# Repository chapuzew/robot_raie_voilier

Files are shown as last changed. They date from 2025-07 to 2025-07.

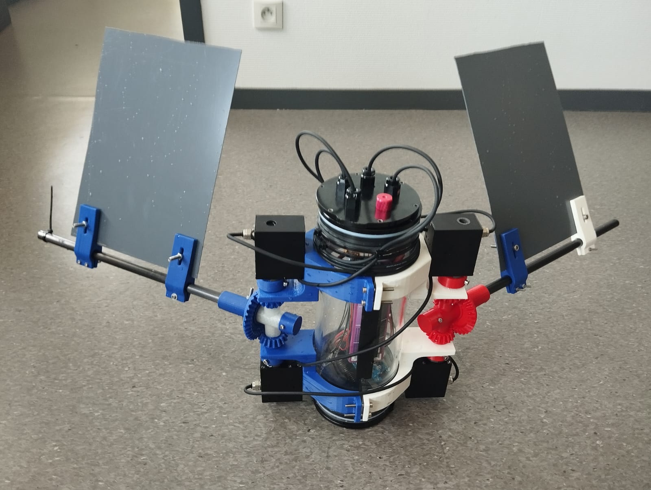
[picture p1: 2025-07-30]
robot_raie.jpg

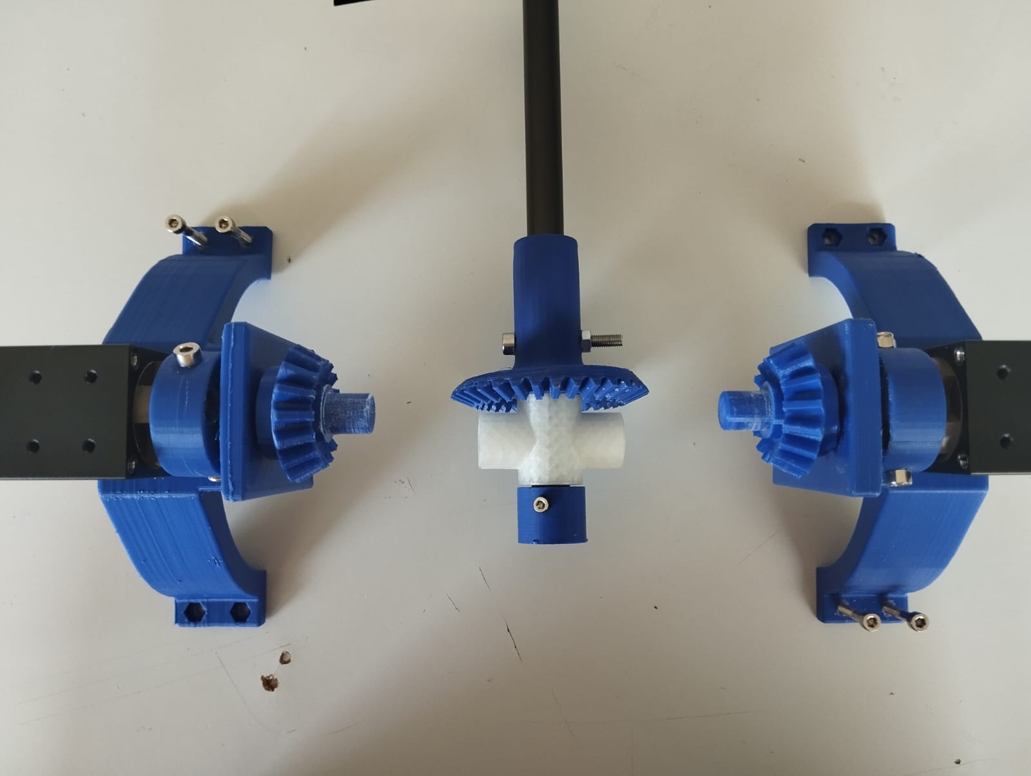
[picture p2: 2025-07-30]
videos-photos/WhatsApp Image 2025-07-22 à 16.33.31_99630c48.jpg

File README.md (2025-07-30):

Ce projet a etait réalisé dans le cadre de ma première année du Master Robotique Aquatique Mobile de l’ENSTA (École nationale supérieure de techniques avancées) Bretagne. Il présente les travaux menés lors d’un stage réalisé au sein du laboratoire de recherche STIC (Laboratoire des Sciences et Technologies de l'Information, de la Communication et de la Connaissance), à Brest, et porte sur le développement d’un prototype de robot bio-inspiré capable d’évoluer dans deux environnements distincts : en surface, à la manière d’un voilier, et sous l’eau, par nage ondulatoire inspirée des raies.
L’objectif principal de ce travail était de concevoir, fabriquer et tester un système capable de combiner ces deux modes de locomotion dans un même robot. L’approche retenue est bio-inspirée, dans le sens où elle s’appuie sur des principes naturels de déplacement, sans chercher à reproduire fidèlement une morphologie existante.
Ce travail avait pour but de déterminer si un prototype fonctionnel combinant ces deux modes de déplacement pouvait constituer une base pertinente pour un développement plus poussé. Une attention particulière a été portée à la conception mécanique, en intégrant dès le départ une contrainte de fabrication locale : toutes les pièces du robot devaient être réalisables via impression 3D ou usinage CNC, en utilisant les moyens disponibles sur place.
Le présent document retrace l’ensemble des étapes de développement, depuis la conception mécanique initiale jusqu’aux expérimentations finales en milieu aquatique. Il détaille également l’architecture électronique embarquée, les choix logiciels effectués (communication, contrôle des moteurs), ainsi que les observations et pistes d’amélioration identifiées à l’issue des essais en bassin.

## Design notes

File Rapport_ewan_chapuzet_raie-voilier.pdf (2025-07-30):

# Prototype d’un robot hybride de navigation multi-milieux : propulsion ondulatoire et voiles

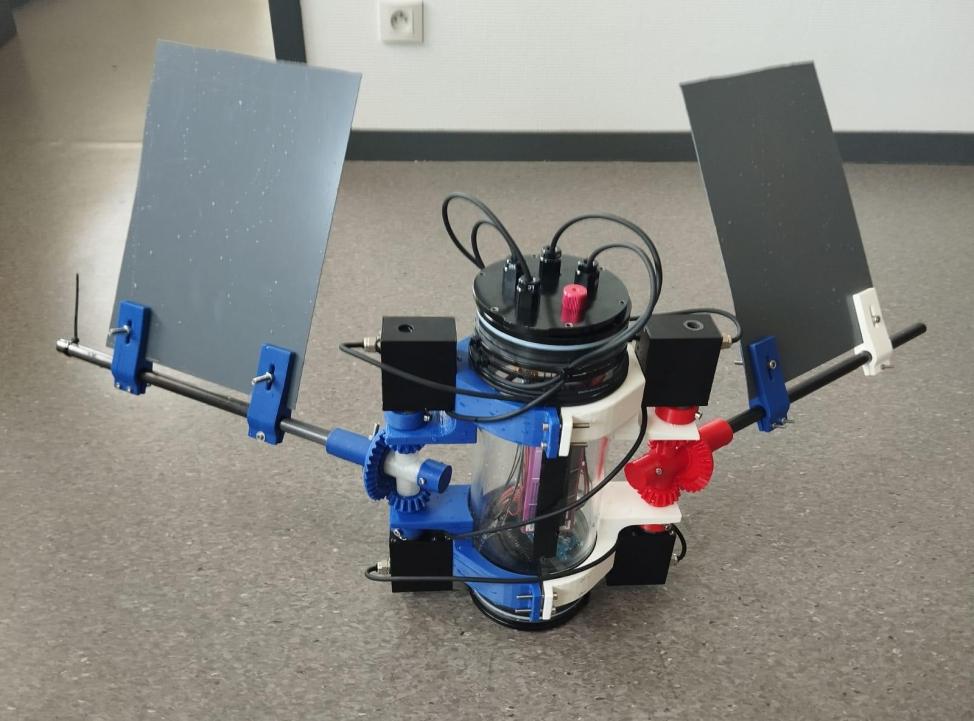
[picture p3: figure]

Figure 1 : Robot raie-voilier
Ce rapport s’inscrit dans le cadre de ma première année du Master Robotique Aquatique Mobile de l’ENSTA (École nationale supérieure de techniques avancées) Bretagne. Il présente les travaux menés lors d’un stage réalisé au sein du laboratoire de recherche STIC (Laboratoire des Sciences et Technologies de l'Information, de la Communication et de la Connaissance), à Brest, sous la supervision de Loick Degorre et Lionel Lapierre. Ce stage porte sur le développement d’un prototype de robot bio-inspiré capable d’évoluer dans deux environnements distincts : en surface, à la manière d’un voilier, et sous l’eau, par nage ondulatoire inspirée des raies. L’objectif principal de ce travail était de concevoir, fabriquer et tester un système capable de combiner ces deux modes de locomotion dans un même robot. L’approche retenue est bio-inspirée, dans le sens où elle s’appuie sur des principes naturels de déplacement, sans chercher à reproduire fidèlement une morphologie existante.
Ce travail avait pour but de déterminer si un prototype fonctionnel combinant ces deux modes de déplacement pouvait constituer une base pertinente pour un développement plus poussé. Une attention particulière a été portée à la conception mécanique, en intégrant dès le départ une contrainte de fabrication locale : toutes les pièces du robot devaient être réalisables via impression 3D ou usinage CNC, en utilisant les moyens disponibles sur place.
Le présent document retrace l’ensemble des étapes de développement, depuis la conception mécanique initiale jusqu’aux expérimentations finales en milieu aquatique. Il détaille également l’architecture électronique embarquée, les choix logiciels effectués (communication, contrôle des moteurs), ainsi que les observations et pistes d’amélioration identifiées à l’issue des essais en bassin.

## 1. Prototypage physique du Robot raie-voilier

### 1.1Conception mécanique de l’épaule

Le développement du robot raie-voilier a débuté par le prototypage mécanique de ses deux épaules, placées symétriquement de part et d’autre du tube principal. Inspirée de la nage ondulatoire des raies, cette conception s’inscrit dans une démarche bio-inspirée visant à exploiter les principes naturels de propulsion grâce à des ailes.
Matériaux et composants à disposition Le corps central du robot est constitué d’un tube étanche en polycarbonate de 4 pouces de diamètre et de 30 cm de longueur, fourni avec ses deux embouts ("end caps") et brides ("flanges") compatibles de marque Blue Robotics. Le montage a été réalisé selon les recommandations du Watertight Enclosure User Guide, (https://bluerobotics.com/learn/watertight-enclosure-wte-assembly-new/) garantissant une bonne étanchéité.
L’actionnement des ailes repose sur quatre servomoteurs étanches Rovmaker RM-SV-40, répartis équitablement sur les deux épaules. Les ailes ont été découpées dans des plaques de PVC de 1 mm d’épaisseur. Afin d’optimiser l’adhérence entre les pièces imprimées en 3D et le tube central, des bandes de caoutchouc de 1,5 mm ont été utilisées comme interface souple. Remarque importante : Toutes les pièces imprimées en 3D doivent impérativement respecter les paramètres définis dans la photo "parametres_impression", notamment avec un remplissage à 80 % et avec un motif gyroïde, afin d'assurer une bonne résistance mécanique. Il est également essentiel de veiller à l’orientation correcte des pièces comportant des engrenages lors de l’impression : les dents doivent impérativement être orientées vers le haut, pour garantir une meilleure précision et robustesse de l’ensemble.
Conception de l’épaule
Chaque épaule est conçue pour offrir deux degrés de liberté, dans le but d’explorer une large gamme de configurations tout en limitant la complexité mécanique. Le principe de rotation utilisé s’inspire du mécanisme présenté par thang010146 dans sa vidéo YouTube intitulée “Controlling pan and tilt rotation of an object”.
Les pièces de liaison entre les épaules et le tube central reprennent les principes des clamps Blue Robotics, assurant une fixation solide. Le montage complet est documenté dans le fichier d’assemblage “robot_raie_voilier”, qui répertorie l’ensemble des éléments mécaniques nécessaires, à l’exception de l’électronique, du câble de communication (tether 7 fils), des matériaux d’étanchéité et du filament d’impression 3D.
Améliorations mécaniques
Dans une première version, le mécanisme original a été simplifié par la suppression des courroies, remplacées par un contact direct entre pièces imprimées. Bien que ce système ait montré un fonctionnement correct, il s’est avéré trop fragile pour supporter des efforts importants.

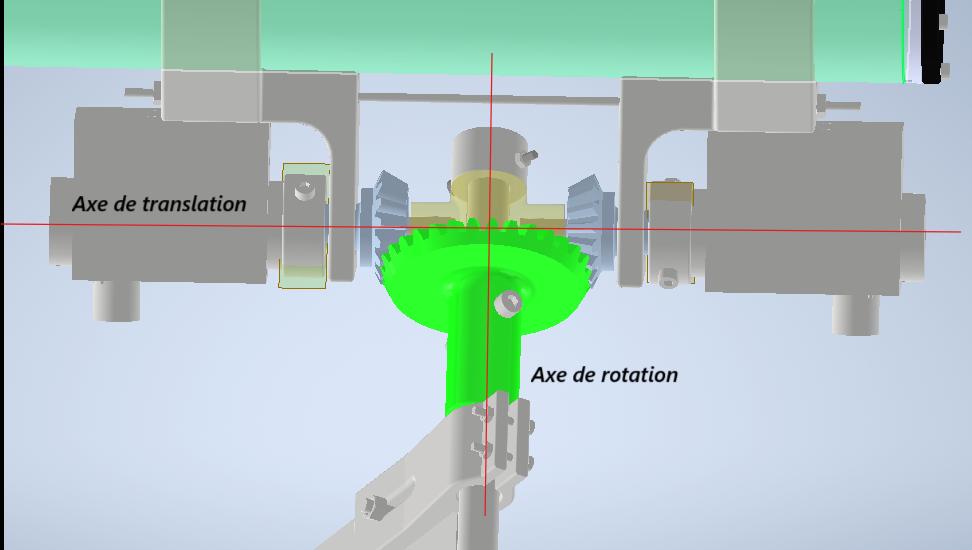
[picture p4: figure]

Figure 2: Axes de liberté de l'épaule
Plusieurs évolutions ont donc été intégrées pour renforcer la robustesse du système :
- Renforcement de l’axe de rotation : l’utilisation du tube en fibre de carbone, qui sert de point d’attache des ailes, comme axe de rotation a permis de mieux supporter les charges mécaniques induites par le mouvement des ailes.
- Renforcement de l’axe de translation : deux pièces en acier ont été ajoutées pour assurer une liaison rigide entre l’axe central et les engrenages commandés par les servomoteurs.
Pour une version allégée sans usinage mécanique, il est possible d’utiliser la pièce “engrenage_secondaire_V2”, moins robuste, en remplacement de la version actuelle “engrenage_secondaire_V3”.

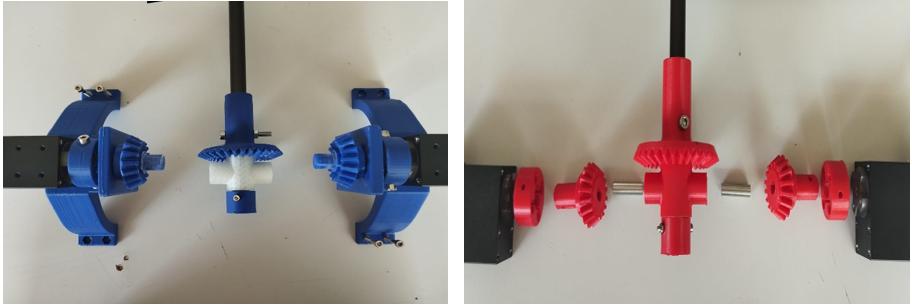
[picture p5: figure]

Figure 3 : Evolution de l’épaule pour son renforcement
Ces modifications ont abouti à une structure mécanique plus fiable et résistante aux chocs, en particulier au niveau de la liaison entre les ailes et les servomoteurs.
Enfin, le fichier “Etapes_de_montage” fournit une procédure détaillée pour l’assemblage du robot de manière reproductible.

### 1.2Architecture électronique

Le système étant conçu pour fonctionner en autonomie, l’alimentation est assurée par deux batteries LiPo 3S (11,1 V), utilisées pour dissocier les alimentations des sous-systèmes et améliorer la fiabilité globale :
- Une batterie LiPo 3S – 2,2 Ah alimente la partie électronique de contrôle, constituée d’une carte Arduino Mega couplée à son shield Ethernet.
- Une batterie LiPo 3S – 5 Ah est dédiée à l’alimentation des quatre servomoteurs étanches Rovmaker.
Il est essentiel de connecter toutes les masses électriques entre elles pour assurer une référence de signal cohérente, notamment entre la carte de commande et les actionneurs.
L’étanchéité des passages de câbles entre l’intérieur du tube et l’extérieur est assurée par des pénétrateurs WetLink de 5,5 mm pour les fils des moteurs. Le tether de 7 fils, utilisé pour la communication externe, passe quant à lui par un pénétrateur étanche de 7,5 mm.
Ces composants garantissent une parfaite étanchéité de la partie immergée tout en assurant la fonctionnalité des câbles de commande et de communication. Leur montage suit les instructions officielles de Blue Robotics (: WetLink Penetrator Installation Guide – Blue Robotics). (https://bluerobotics.com/learn/wetlink-penetrator-installation-guide/)

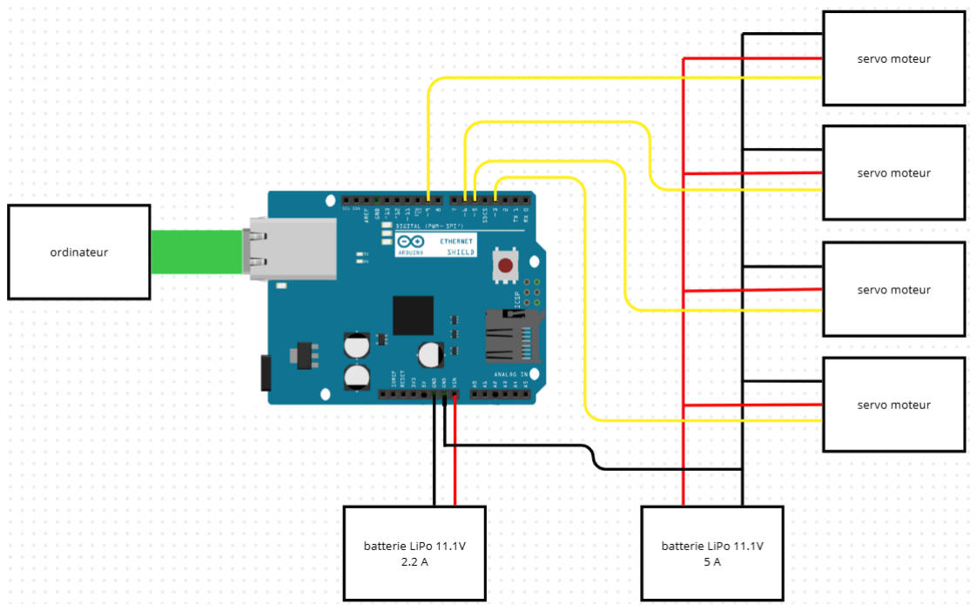
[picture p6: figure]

Figure 4 : Schéma électrique du robot

## 2. Communication et algorithmique embarqués dans le robot raie-voilier

### 2.1Architecture algorithmique

Le développement logiciel du robot raie-voilier a été entièrement réalisé en C++, en s’appuyant sur l’environnement PlatformIO intégré à Visual Studio Code, afin de bénéficier d’un cadre de développement modulaire, compatible avec les microcontrôleurs de type Arduino Mega 2560. L’architecture logicielle repose sur une organisation orientée objet, articulée autour de trois classes principales. Chaque classe remplit un rôle spécifique dans la commande des actionneurs et la gestion de la communication réseau :
Classe Differential
Cette classe constitue la brique de base du contrôle d’une épaule seule. Elle encapsule la logique de génération de signaux pour les servomoteurs étanches, permettant la création de mouvements ondulatoires paramétrables (amplitude, fréquence, phase). Cette structure logicielle a été initialement développée dans un objectif de prototypage rapide, afin de valider les comportements mécaniques élémentaires d’une aile avant l’intégration dans un système plus complexe.
De plus, la classe permet de tester différentes stratégies de locomotion inspirées des nageoires pectorales de la raie, notamment via des profils sinusoïdaux modulables.
Classe DifferentialGroup
Pour permettre la commande synchronisée des deux épaules du robot, une composante logicielle spécifique a été développée : la classe DifferentialGroup. Celle-ci regroupe deux instances indépendantes de la classe Differential, chacune correspondant à une aile, et fournit une interface centralisée permettant de piloter leurs mouvements de manière coordonnée. Cette structure logicielle permet d’implémenter facilement des comportements symétriques (comme des battements d’ailes en miroir) ou asymétriques (par exemple pour induire une direction). Elle joue un rôle essentiel dans la gestion des mouvements complexes, en garantissant une cohérence temporelle et fonctionnelle entre les deux actionneurs.
La classe DifferentialGroup intègre également des fonctions d’initialisation, de calibration, et de synchronisation, assurant que les deux modules répondent correctement aux paramètres définis, qu’ils soient prédéfinis ou transmis dynamiquement via la communication réseau. Classe DifferentialServer
Enfin, la gestion de la communication réseau est assurée par la classe DifferentialServer. Celle-ci met en œuvre un serveur TCP/IP embarqué sur l’Arduino, configuré pour recevoir des commandes externes via liaison Ethernet. Elle assure la réception, l’interprétation, et le routage des messages vers les fonctions correspondantes du système de commande.
Cette approche permet une séparation claire entre les couches réseau, logique de commande, et pilotage matériel, facilitant la maintenance, la réutilisation et l’extension future du code embarqué.

Fichier main.cpp
Le fichier principal du projet (main.cpp) agit comme orchestrateur du système. Il initialise les objets des différentes classes, configure les entrées/sorties matérielles, et exécute la boucle principale du programme. Cette dernière repose sur un mécanisme d’écoute passive, en attente de paquets réseau, permettant de réagir dynamiquement aux instructions utilisateur.

### 2.2Méthode de communication

Choix de la technologie
La communication entre l’utilisateur et le robot a été mise en œuvre via une liaison Ethernet filaire, à travers un tether 7 fils étanche connecté au shield Ethernet de la carte Arduino Mega 2560. Ce choix technologique a été guidé par des considérations de robustesse, de simplicité de mise en œuvre, et d’interopérabilité avec les outils de diagnostic réseau existants. Fonctionnement général
Le protocole de communication repose sur TCP/IP, avec une architecture client-serveur dans laquelle le robot agit comme serveur. Le fonctionnement général peut être résumé en plusieurs étapes :
1. Initialisation réseau
Lors de la mise sous tension, le robot initialise son interface réseau avec une adresse IP statique (par exemple, 192.168.1.177) et ouvre un port d’écoute (par défaut le port 80). Le système est alors prêt à recevoir des requêtes entrantes.
2. Configuration du poste utilisateur
L’ordinateur de commande doit être connecté directement au tether. Une configuration réseau manuelle est nécessaire :
- IP : 192.168.1.1
- Masque : 255.255.255.0
- Passerelle : 192.168.1.1 Cette configuration permet de placer les deux dispositifs dans le même sous-réseau local, éliminant le besoin d’un routeur ou d’un service DHCP.
3. Envoi des commandes
Les commandes sont envoyées sous forme de chaînes de caractères via la commande ‘curl’, ou via des scripts utilisant ce protocole. Le fichier « commandes.txt » fourni regroupe les exemples de commandes utilisables.
4. Traitement embarqué
Les messages reçus sont interprétés par DifferentialServer pour en extraire les instructions correspondantes (ex. démarrage, arrêt, changement de fréquence), puis transmis à la classe DifferentialGroup pour exécution.
5. Retour d’informations (futur développement)
Bien que non encore pleinement implémentée, la structure actuelle permet le retour de messages de diagnostic ou de confirmation vers l’utilisateur. Cette fonctionnalité ouvre la voie à la mise en place future d’interfaces de supervision graphique ou de télémétrie en temps réel grâce à l’implémentation de capteurs sur le robot.

## 3. Analyse critique et perspectives d'amélioration

### 3.1Observations générales

Les premiers essais fonctionnels du robot ont été réalisés au sein du bassin de test du laboratoire, à l’aide de la version finale du prototype. Deux campagnes d’essais ont été menées, permettant d’évaluer le comportement du système dans différents états d’équilibrage et sous différentes sollicitations mécaniques.
Lors de ces tests, plusieurs constats ont pu être établis concernant la stabilité, la réponse mécanique du système, et la capacité de déplacement dans le milieu aquatique.
Flottabilité et équilibre
Dans sa configuration initiale, le robot présente une flottabilité importante, conduisant à un déséquilibre latéral (droite-gauche), notamment du fait que les moteurs sont en grande partie situés hors de l’eau. Ce déséquilibre nuit à la stabilité en surface et rend les essais moins représentatifs.
Sur l’axe longitudinal (avant-arrière), la stabilité du robot dépend fortement de la position des épaules sur le tube central. Or, ce réglage est délicat à ajuster avec précision, et constitue un point limitant pour obtenir un comportement stable sans système actif de correction.
Deux états du robot ont été testés afin de comparer leurs effets sur la stabilité et le déplacement :
- État 1 : Robot sans lest additionnel. Flottabilité très élevée, avec un niveau d’immersion correspondant à la moitié du corps. Légère instabilité vers l’arrière.
- État 2 : Robot avec ajout de poids internes. Flottabilité importante mais assez faible pour permettre l’immersion via un actionnement moteurs. Niveau d’eau situé aux trois quarts du corps. Instabilité déplacée vers l’avant.
Ces deux configurations ont permis de mieux comprendre l’influence du centre de masse et du volume immergé sur la dynamique du robot.
Comportement mécanique et limites des actionneurs
D’un point de vue mécanique, l’ensemble du système s’est montré fonctionnel et résistant aux efforts appliqués durant les tests. Néanmoins, il a été observé que dans certaines conditions de charge, les moteurs semblent légèrement dévier de leur position cible, comme si un delta angulaire était appliqué pour limiter la contrainte et éviter la casse mécanique. Cette observation suggère que les moteurs atteignent leur limite de couple et ne peuvent maintenir leur consigne face à une opposition trop importante. Une étude approfondie serait nécessaire pour évaluer la puissance réelle disponible et l’efficacité de l’actionnement dans différents régimes. Également, en configuration de nage ondulatoire (type raie), le robot présente une légère tendance à dériver du côté du tether de communication, probablement en raison de la traînée induite par celui-ci.

Évaluation des schémas de mouvement
Plusieurs profils de commande ont été testés afin d’évaluer les performances du robot dans différentes configurations d’excitation (fréquence, amplitude, combinaison des axes). Chaque essai a été noté sur une échelle de 0 à 10, où 0 représente un déplacement nul ou non contrôlé, et 10 un déplacement fluide, continu, et approximativement rectiligne.
Les résultats des tests sont présentés dans le tableau suivant :
Courbe de mouvement des ailes | | Etat 1 | Etat 2
| Basse fréquence / amplitude moyenne (40°) | Déplacement propre avec une avancée correcte grâce à la déformation de l’extrémité interne de l’aile. (8/10) | Déplacement difficile avec le mouvement du corps dû à la poussée des ailes. La force étant transmise dans le corps (sous forme d’oscillation dans le sens de la longueur), les ailes ne se déforment pas, ce qui ne permet pas d’avancer. (1.5/10)
| Voies d’améliorations | Mettre une aile plus souple pour permettre une meilleure poussée. | Modifier les ailes (plus petites ou bien plus souples) ou stabiliser le corps (alourdir ou rajouter une quille) pour que la force entraîne un déplacement.
| Haute fréquence / basse amplitude (20°) | Déplacement saccadé avec beaucoup de perte d’énergie pour peu de déplacement. (4.5/10) | Déplacement présent mais pas optimum. Le corps n’ayant pas le temps de dépenser l’énergie transmise par les ailes dû à la haute fréquence, l’ensemble se déplace. Le robot a réussi à plonger certaines fois malgré une flottabilité non neutre. (6/10)
| Voies d’améliorations | Ailes moins élastiques pour permettre une meilleure poussée. | Alourdir le corps pour une plus faible perte d’énergie.
Sinusoïde en translation + rotation (25°) Remarque : à haute amplitude de rotation, le système ne retransmet pas bien les force et les mouvements ne permets pas le placement. | Basse fréquence / amplitude translation moyenne (40°) | Déplacements très faibles et partiellement aléatoires. Grande perte d’énergie avec le déplacement du corps dans le sens de la longueur. (2/10) | Très peu de déplacement avec toute la force perdue par l’oscillation du corps. (3/10)
| Voies d’améliorations | Stabiliser le corps avec une quille ou des flotteurs si on veut un mouvement à la surface de l’eau. | Stabiliser le corps (alourdir ou rajouter une quille) ou redimensionner les ailes (plus petites ou bien plus souples) pour permettre une meilleure transmission des forces pour le déplacement.
Sinusoïde | en
translation

Haute fréquence
/ | basse
amplitude | de
translation (20°)

Mouvement quasiment
nul et non orienté.
Mouvement | de
l’ensemble dans tous
les sens. (1/10)
Déplacement | faible | et
partiellement | chaotique.
(3.5/10)

Les essais ont mis en évidence une forte variabilité des performances selon les états du robot et les paramètres d’entrée. On note notamment que :
- En mode sinusoïde purement translationnel, des déplacements significatifs ont pu être obtenus en basse fréquence et amplitude moyenne, particulièrement en État 1 (8/10). Toutefois, ce mouvement devient moins efficace en État 2, où les oscillations longitudinales du corps absorbent l’énergie, empêchant les ailes de se déformer correctement (1.5/10).
- Les profils à haute fréquence et faible amplitude génèrent des déplacements plus chaotiques, souvent avec des pertes d’énergie importantes dues à la raideur du système (résultats entre 4 et 6/10 selon l’état).
- En ajoutant une composante rotative aux mouvements des ailes, les performances se sont globalement dégradées, en raison d’une mauvaise transmission des forces au corps du robot. Les déplacements sont alors faibles, désordonnés, voire inexistants dans certains cas.
Malgré des performances perfectibles, ces essais ont permis de valider le principe fonctionnel du système hybride, avec un déplacement mesurable à la fois en surface et en immersion. Le système reste toutefois perfectible, notamment sur le plan de la stabilité passive, de l’optimisation de la poussée des ailes, et de la configuration des masses.
Remarques sur le mode voilier
Bien que les essais n’aient pas encore été menés dans un scénario complet de navigation en surface (type voilier), il a été vérifié que le robot est capable de relever les ailes et de les orienter. Cependant, on observe un enfoncement du corps d’environ 5 cm sous la ligne de flottaison, ce qui entraîne une instabilité modérée. En l’absence de perturbations, le robot reste partiellement stable en statique, mais l’ensemble reste à affiner avant des essais dynamiques avec vent simulé ou propulsion par voile.

### 3.2Axes d'amélioration

À l’issue des essais réalisés, plusieurs pistes d’évolution ont été identifiées, tant sur le plan matériel que fonctionnel. Ces propositions visent à améliorer la stabilité, l’efficacité de la propulsion ainsi que la maniabilité du robot dans ses différents environnements (surface, immersion partielle, pleine immersion).
Évolution du système matériel L’ajout d’un ballast contrôlable constitue la principale amélioration envisagée à court terme. Il permettrait de gérer dynamiquement la profondeur et la flottabilité du robot, offrant ainsi une plus grande liberté de manœuvre. Toutefois, cet ajout impliquerait un déséquilibre de masse, qui devra être compensé soit par une masse amovible symétriquement opposée au ballast, soit par un système de volant d’inertie. Il peut aussi être envisageable d'exploiter ce déséquilibre pour induire une inclinaison contrôlée vers l’avant ou l’arrière, potentiellement utile à la propulsion. Une autre évolution importante consisterait à remplacer la liaison filaire (tether) par un système de communication sans fil (radio ou acoustique), afin de supprimer les contraintes induites par la traînée du câble à l’arrière. Si cette liaison reste indispensable, il conviendrait au minimum de centrer le tether sur la partie arrière du robot (notamment via la "tape" prévue à cet effet), afin que sa résistance se traduise uniquement par un ralentissement global et non par une perturbation de la trajectoire.
En ce qui concerne la structure existante, les clamps fixant les épaules pourraient être usinées en plusieurs parties afin d’améliorer leur rigidité et leur durabilité. À ce jour, les engrenages imprimés en 3D ne présentent pas de signes de faiblesse, mais une version usinée pourrait à terme garantir une fiabilité accrue en conditions extrêmes.
Optimisation de la propulsion L’analyse des essais en bassin a montré que le mouvement ondulatoire de grande amplitude à basse fréquence (notamment en État 1) générait un déplacement efficace en surface, en tirant parti de la déformation naturelle des ailes. À l’inverse, en immersion (État 2), le déplacement était meilleur avec des battements rapides de faible amplitude, car le corps du robot absorbait moins l’énergie transmise.
Ainsi, une fois la stabilité longitudinale assurée (via quille, ballast ou fuselage), il pourrait être pertinent de privilégier des ailes plus souples, capables de se déformer davantage pour amplifier le mouvement ondulatoire à basse fréquence, comme observé chez certaines espèces de raies. En fonction des résultats, un redimensionnement des ailes (en réduisant ou augmentant leur surface) pourrait aussi être envisagé.
Recherche de stabilité
Quel que soit le mode de fonctionnement – en surface, partiellement immergé ou complètement sous l’eau – la stabilité du corps reste un facteur déterminant. L’ajout d’un fuselage ou d’une quille pourrait fortement contribuer à stabiliser l’ensemble, tant en roulis qu’en tangage, facilitant ainsi la propulsion rectiligne.
Enfin, une modification de la géométrie du robot pourrait être bénéfique : reculer la base des épaules sur le corps, tout en ajoutant une masse à l’avant, permettrait de déplacer le centre de poussée vers l’arrière, et donc de mieux stabiliser la direction et l’efficacité de la propulsion.

## Conclusion

Ce projet s’inscrit dans une démarche visant à concevoir un robot bio-inspiré capable de se déplacer efficacement à la fois sous l’eau, en imitant les mouvements d’une raie, et en surface, à la manière d’un voilier. L’ensemble du travail mené au cours de ce stage a permis de poser les bases d’un prototype fonctionnel, tout en respectant les contraintes de fabrication locale et de simplicité mécanique.
La phase de conception a abouti à une structure robuste, imprimable en 3D, intégrant des épaules à deux degrés de liberté permettant une large variété de mouvements. L’architecture électronique, embarquée et autonome, a été pensée pour être modulaire et adaptable à différents modes de fonctionnement. Une attention particulière a été portée à l’optimisation mécanique : plusieurs itérations ont été nécessaires pour améliorer la résistance des engrenages et l'efficacité du montage, jusqu’à obtenir un système suffisamment solide pour supporter les efforts générés par les phases de propulsion.
Les essais réalisés en bassin ont permis d’évaluer le comportement du robot dans deux états distincts : avec et sans lest. Ils ont mis en évidence plusieurs configurations de battement d’ailes, montrant que certains paramètres comme la fréquence, l’amplitude et la souplesse des ailes influencent fortement le déplacement obtenu. Bien que le robot ne se déplace pas encore de manière autonome, les tests ont montré qu’un mouvement cohérent et exploitable est atteignable. Dans certaines conditions, des déplacements fluides et réguliers ont été observés, démontrant la faisabilité d’une locomotion efficace sous l’eau. La stabilité du robot reste toutefois à améliorer, notamment sur le plan longitudinal et latéral, en lien avec le placement des moteurs, l'équilibre général et la forme du corps.
Ces observations ont permis de faire émerger plusieurs axes d’amélioration :
- L’ajout d’un système de ballast permettrait de contrôler activement la flottabilité et la profondeur du robot.
- Un changement de système de communication (pour remplacer le tether filaire) pourrait réduire les perturbations sur la trajectoire et améliorer la maniabilité, notamment en surface.
- Le renforcement des pièces mécaniques, notamment par usinage ou redécoupage des clamps, permettrait d’augmenter la durabilité à long terme.
- Un ajustement de la géométrie (recul des ailes, ajout de fuselage ou de quille) pourrait aider à améliorer la stabilité et l’efficacité de la propulsion.
- Enfin, le choix de matériaux plus souples ou le redimensionnement des ailes pourrait optimiser la poussée dans des conditions spécifiques, comme une nage ample à basse fréquence, qui semble être la plus prometteuse pour ce type de déplacement.
En conclusion, le prototypage s’est avéré concluant. Le robot a montré qu’il pouvait déjà fonctionner efficacement en tant que raie, avec un comportement stable et des performances intéressantes dans certaines configurations. Même si sa fonction de voilier n’a pas encore pu être entièrement testée, les résultats obtenus ouvrent de réelles perspectives. Il serait pertinent de poursuivre le développement du système vers un prototype plus abouti, intégrant une meilleure stabilisation, un contrôle autonome et une optimisation fine des paramètres mécaniques. Ce robot pourrait ainsi devenir une plateforme expérimentale polyvalente, adaptée à l’exploration ou à la surveillance en milieu aquatique.

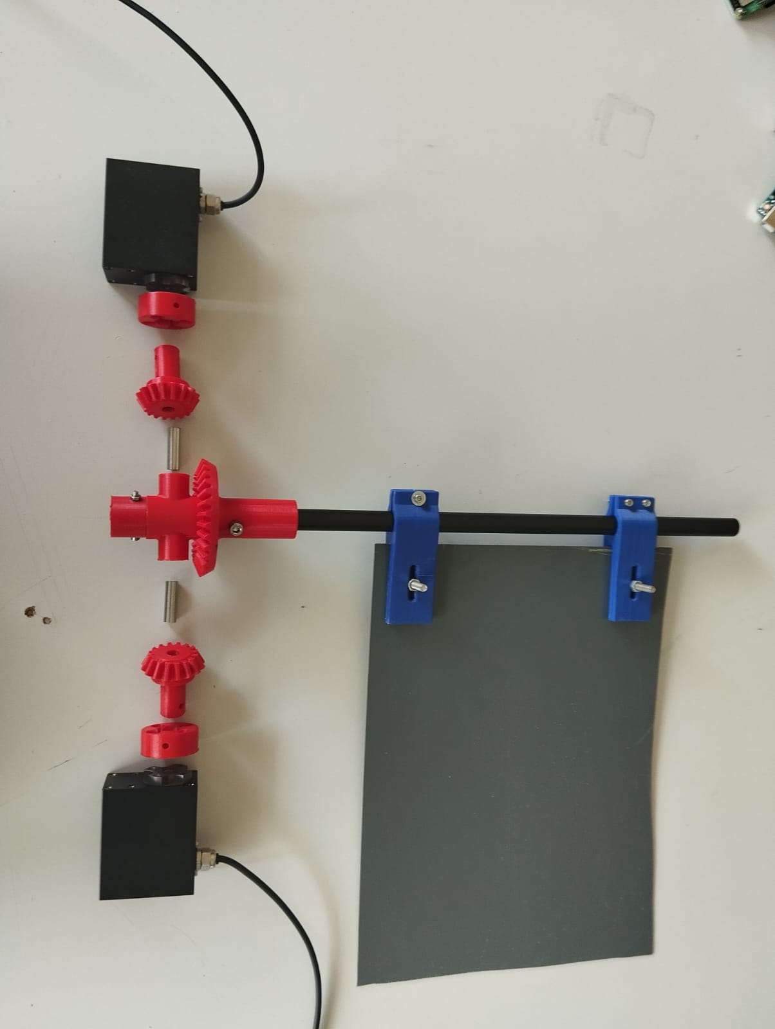
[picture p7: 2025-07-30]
videos-photos/WhatsApp Image 2025-07-22 à 16.33.30_8e47ebda.jpg

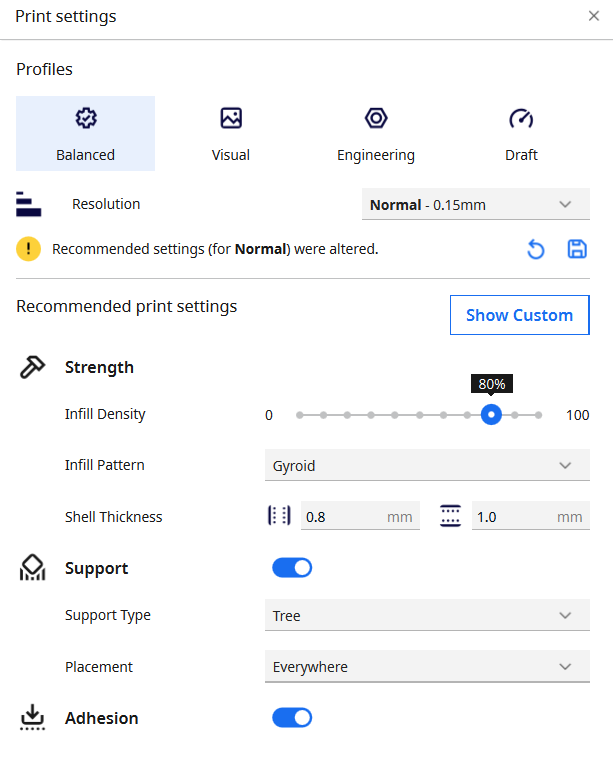
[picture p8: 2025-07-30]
mecanique_robot_raie/impression/parametres_impressions.png

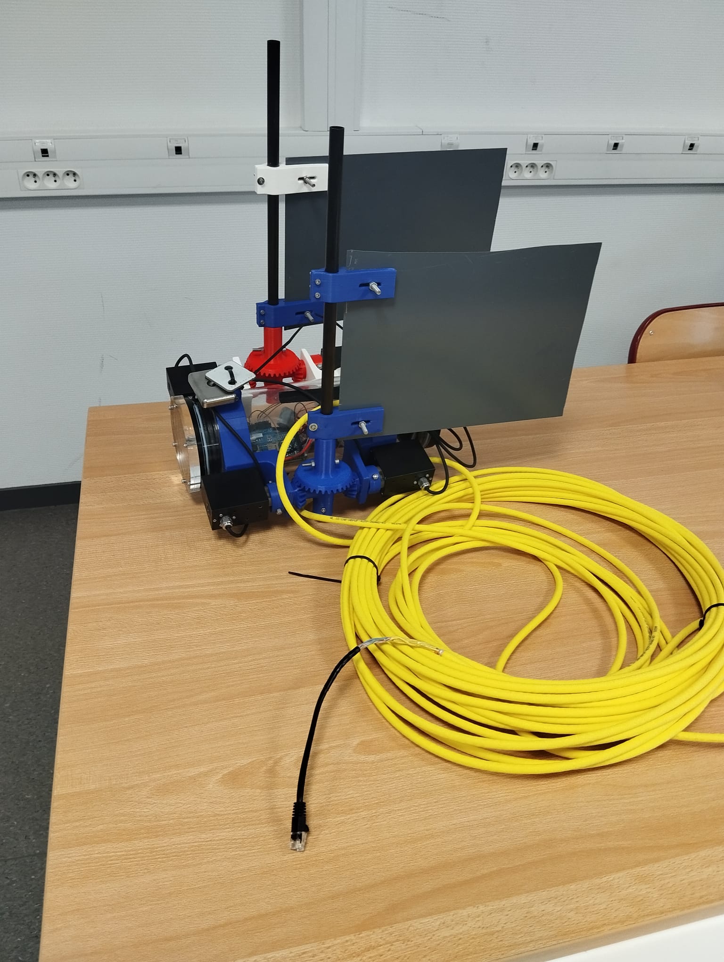
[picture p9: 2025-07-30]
videos-photos/WhatsApp Image 2025-07-22 à 16.32.00_d53e991b.jpg

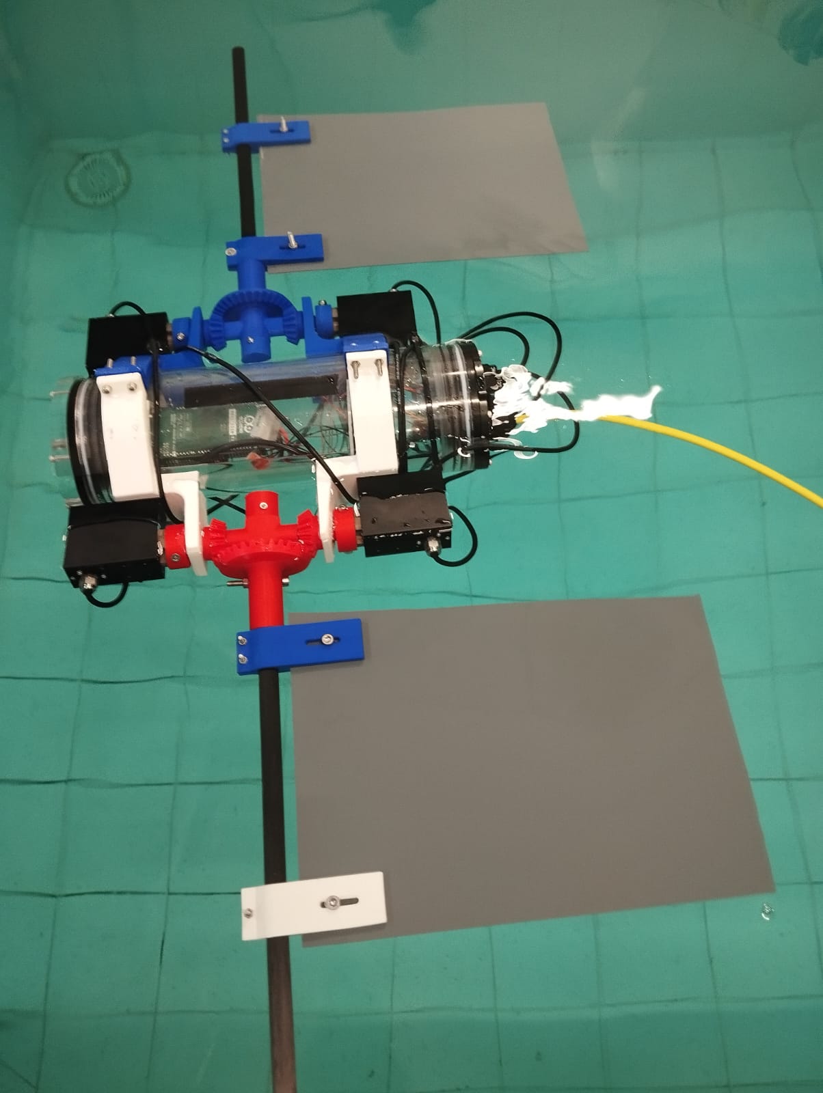
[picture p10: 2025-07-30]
videos-photos/WhatsApp Image 2025-07-22 à 16.31.52_6d24bb8f.jpg

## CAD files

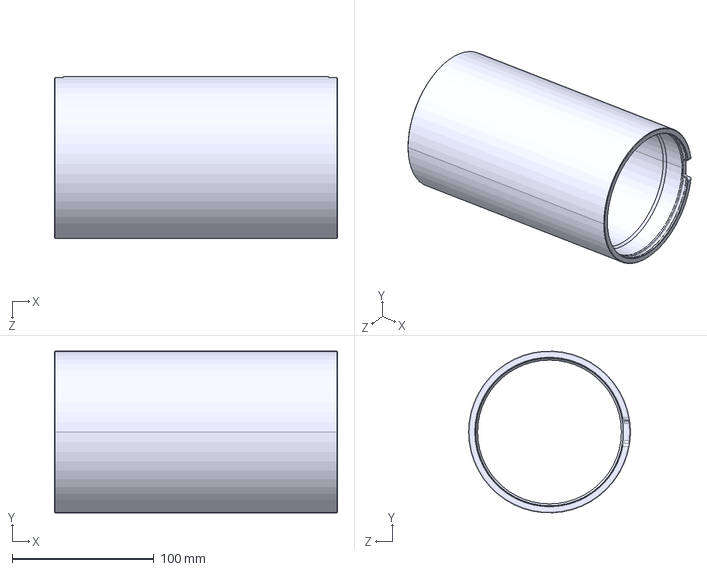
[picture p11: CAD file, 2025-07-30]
mecanique_robot_raie/base_meca/pieces_bluerobotique_reference/WTE4_ACRYLIC_TUBES_BR-101052-XXX/BR-101052-200_RevB/BR-101052-200_RevB.STEP
200.0 x 114.2 x 114.3 mm

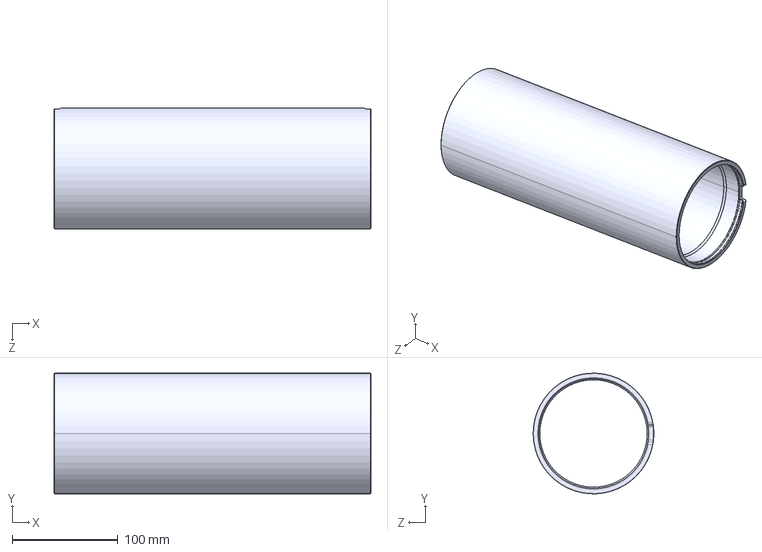
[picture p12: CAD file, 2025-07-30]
mecanique_robot_raie/base_meca/pieces_bluerobotique_reference/WTE4_ACRYLIC_TUBES_BR-101052-XXX/BR-101052-300_RevB/BR-101052-300_RevB.STEP
300.0 x 114.2 x 114.3 mm

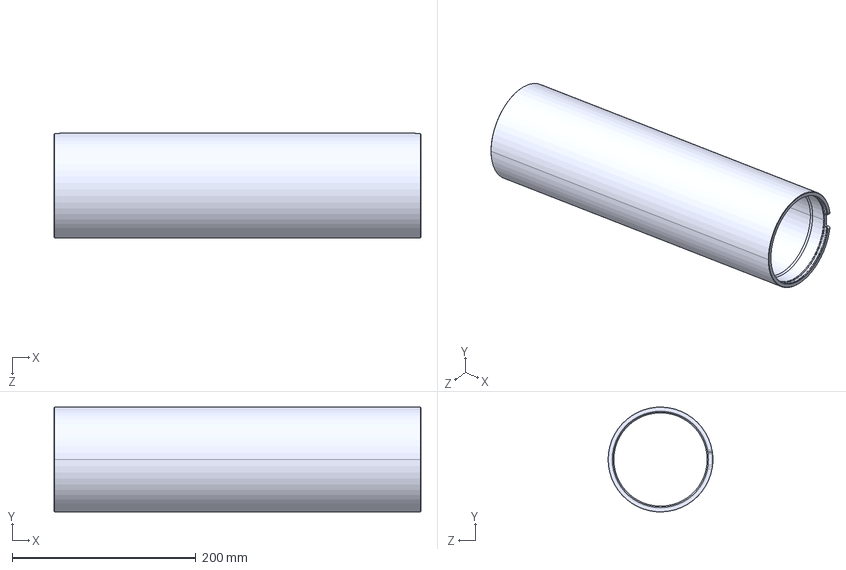
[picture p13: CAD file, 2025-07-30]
mecanique_robot_raie/base_meca/pieces_bluerobotique_reference/WTE4_ACRYLIC_TUBES_BR-101052-XXX/BR-101052-400_RevB/BR-101052-400_RevB.STEP
400.0 x 114.2 x 114.3 mm

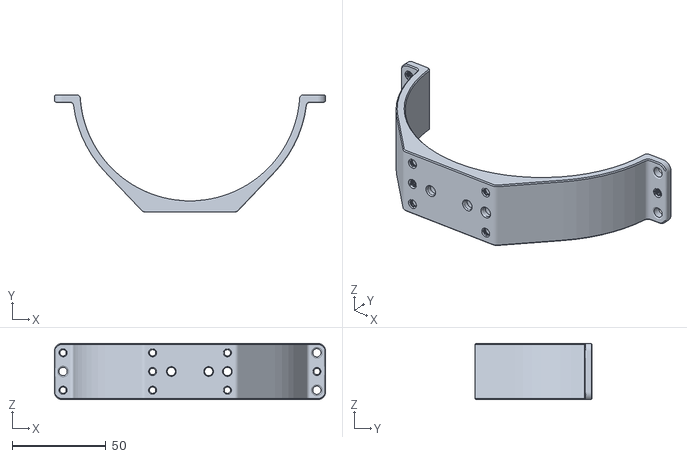
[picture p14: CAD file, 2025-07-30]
mecanique_robot_raie/base_meca/pieces_bluerobotique_reference/WTE4_CLAMP_BR-102710-004/BR-102678-004_RevC.STL
144.9 x 62.8 x 30.0

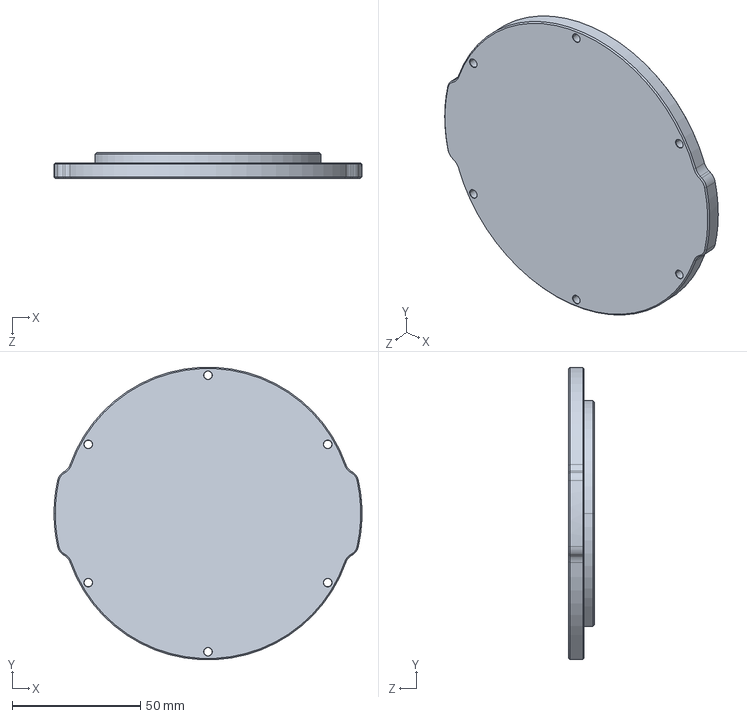
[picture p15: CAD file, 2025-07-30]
mecanique_robot_raie/base_meca/pieces_bluerobotique_reference/WTE4_END_CAP_BLANK_BR-102993-999/WTE4-M-END-CAP-BLANK-R2.step
120.3 x 114.1 x 10.0 mm

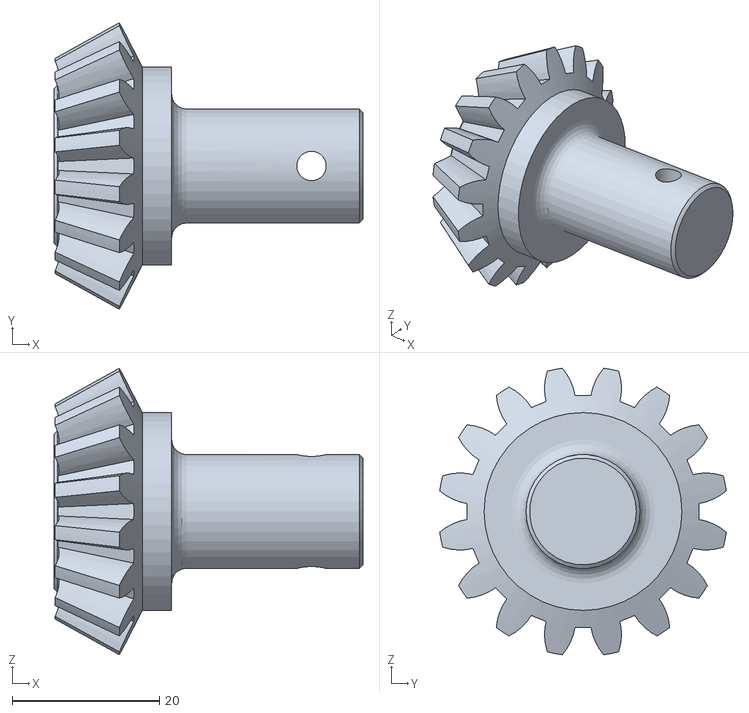
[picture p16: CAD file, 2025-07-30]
mecanique_robot_raie/impression/engrenage_secondaire_v3.stl
42.0 x 39.0 x 39.0

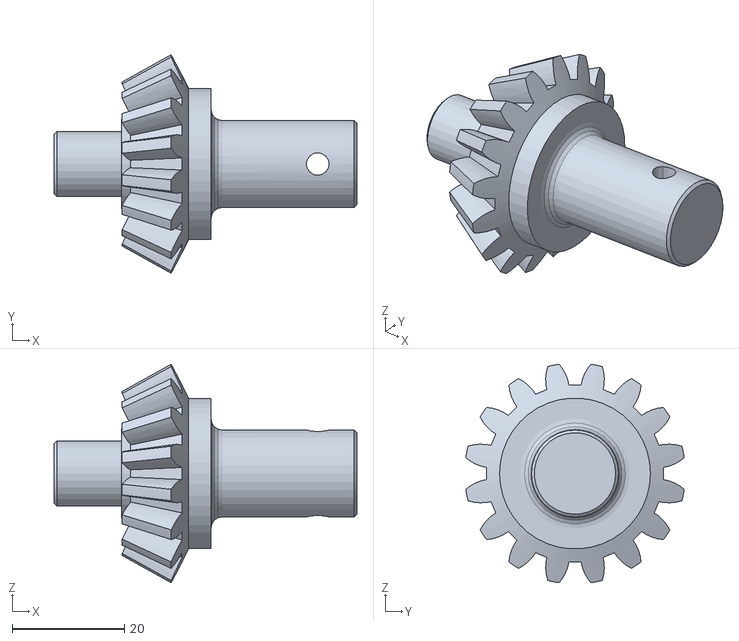
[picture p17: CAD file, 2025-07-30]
mecanique_robot_raie/impression/hold_version/engrenage_secondaire_v2.stl
54.0 x 39.0 x 39.0

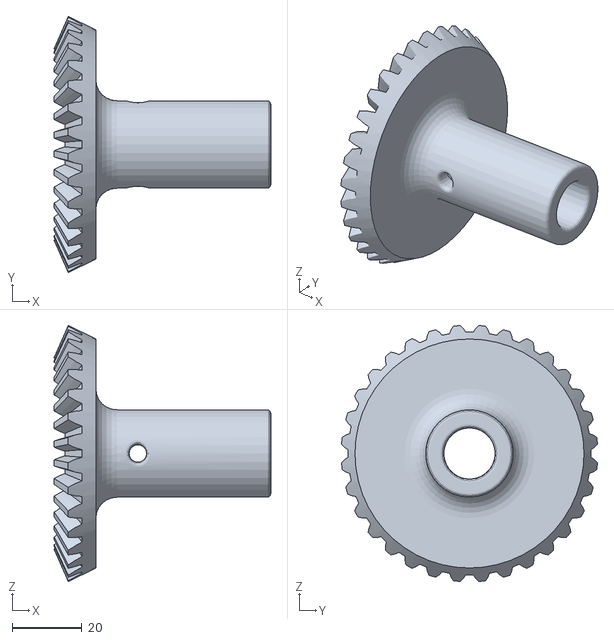
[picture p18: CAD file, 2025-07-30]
mecanique_robot_raie/impression/axe_central.stl
61.9 x 73.2 x 73.2

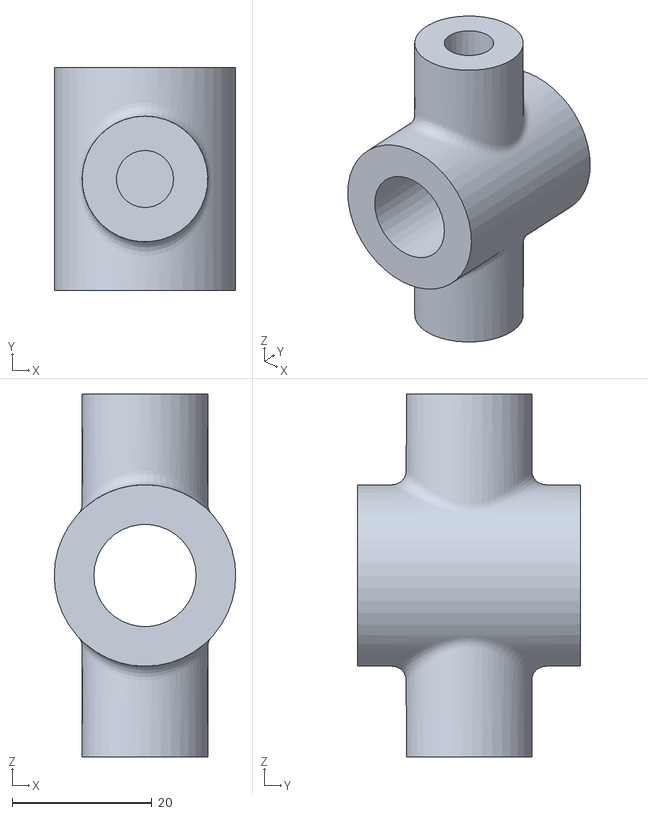
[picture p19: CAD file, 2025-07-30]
mecanique_robot_raie/impression/Cross.stl
26.0 x 32.0 x 52.0

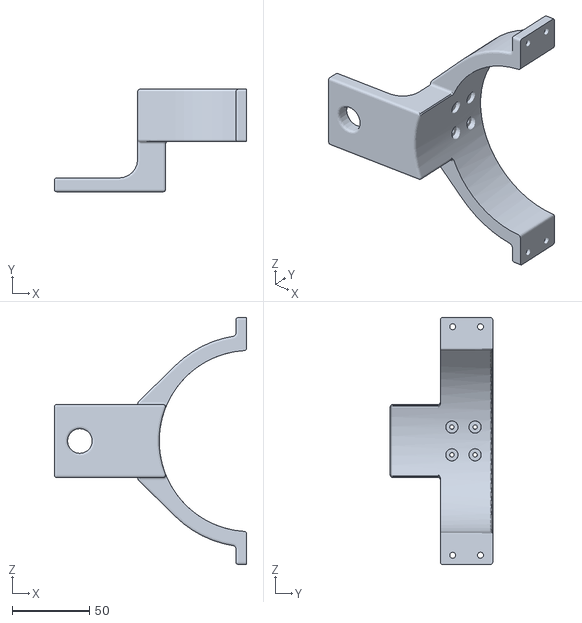
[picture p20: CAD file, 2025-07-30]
mecanique_robot_raie/impression/clamp_v2.stl
124.7 x 66.5 x 160.0

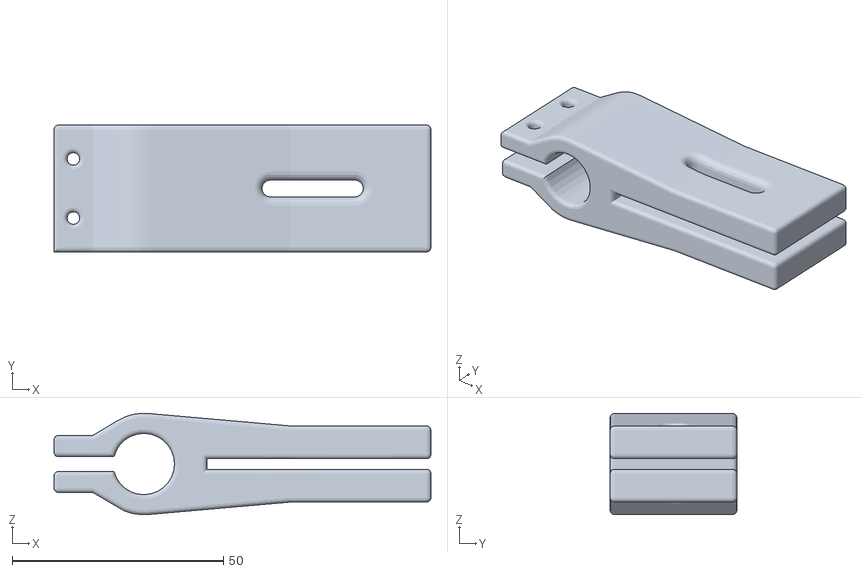
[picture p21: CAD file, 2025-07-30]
mecanique_robot_raie/impression/jonction_aile_axe_centrale.stl
89.2 x 30.0 x 23.9

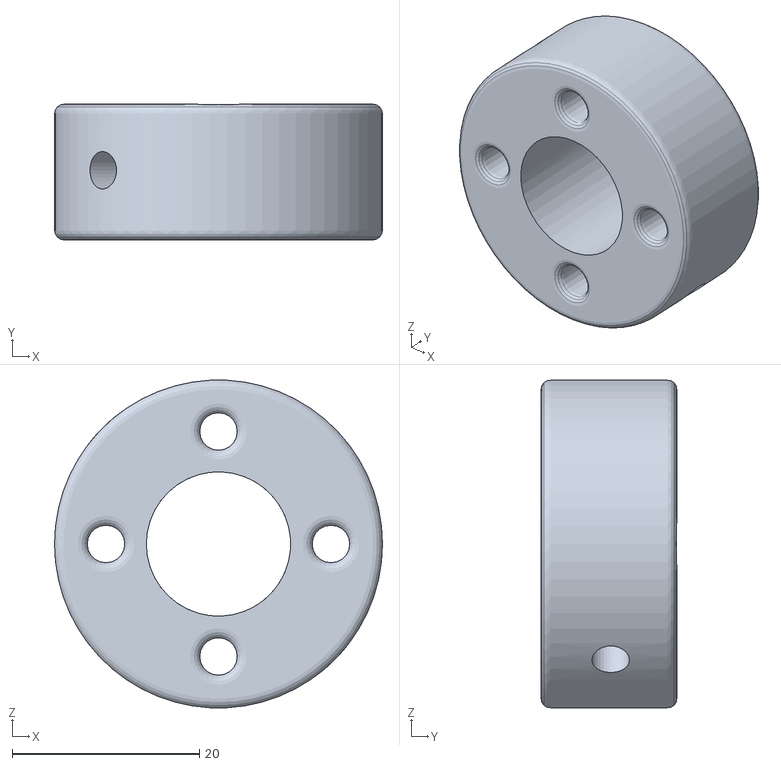
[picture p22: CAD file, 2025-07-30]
mecanique_robot_raie/impression/fixation_harbre_moteur_v2.stl
35.0 x 14.5 x 34.9

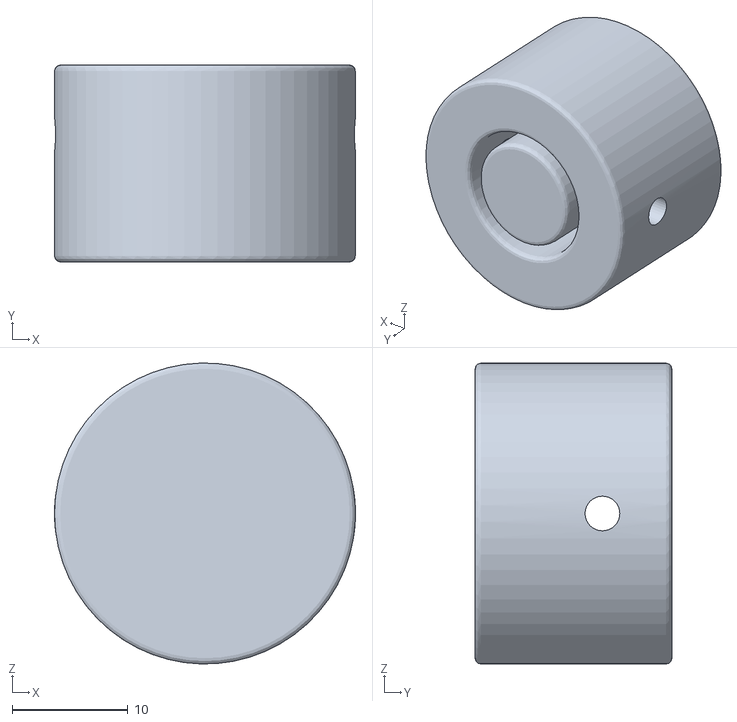
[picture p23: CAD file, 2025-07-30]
mecanique_robot_raie/impression/attache_finaxe_central.stl
26.0 x 17.0 x 26.0

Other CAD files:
mecanique_robot_raie/base_meca/Servo_moteur_rovmaker_RM_SV_40.ipt
mecanique_robot_raie/base_meca/pieces_bluerobotique_reference/WTE4_ACRYLIC_TUBES_BR-101052-XXX/BR-101052-200_RevB/BR-101052-200_RevB.STL
mecanique_robot_raie/base_meca/pieces_bluerobotique_reference/WTE4_ACRYLIC_TUBES_BR-101052-XXX/BR-101052-300_RevB/BR-101052-300_RevB.STL
mecanique_robot_raie/base_meca/pieces_bluerobotique_reference/WTE4_ACRYLIC_TUBES_BR-101052-XXX/BR-101052-300_RevB/BR-101052-300_RevB.ipt
mecanique_robot_raie/base_meca/pieces_bluerobotique_reference/WTE4_ACRYLIC_TUBES_BR-101052-XXX/BR-101052-400_RevB/BR-101052-400_RevB.STL
mecanique_robot_raie/base_meca/pieces_bluerobotique_reference/WTE4_ACRYLIC_TUBES_BR-101052-XXX/BR-101052-400_RevB/BR-101052-400_RevB/BR-101052-400_RevB/BR-101052-400_RevB.ipt
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

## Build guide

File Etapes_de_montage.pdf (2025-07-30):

# Montage mécanique du robot raie voilier

Ce document s’inscrit dans le cadre du développement d’un robot bio-inspiré multi-milieu, capable d’évoluer à la fois en surface, à la manière d’un voilier, et sous l’eau, par propulsion ondulatoire.
Il présente exclusivement le montage mécanique du prototype, à partir des éléments conçus, imprimés et usinés localement, et en s’appuyant sur l’assemblage CAO intitulé « robot_raie_voilier ».
Le robot est construit autour d’un tube étanche en polycarbonate de 4 pouces de diamètre et de 30 cm de longueur (Blue Robotics), fermé à ses extrémités par deux embouts ("end caps") et brides ("flanges") de la même marque, assurant l’étanchéité via des pénétrateurs WetLink. Il intègre quatre servomoteurs étanches Rovmaker RM-SV-40, montés sur des structures réalisées par impression 3D, et deux ailes articulées fixées à un mât en carbone.

## 1. Montage des attaches moteurs

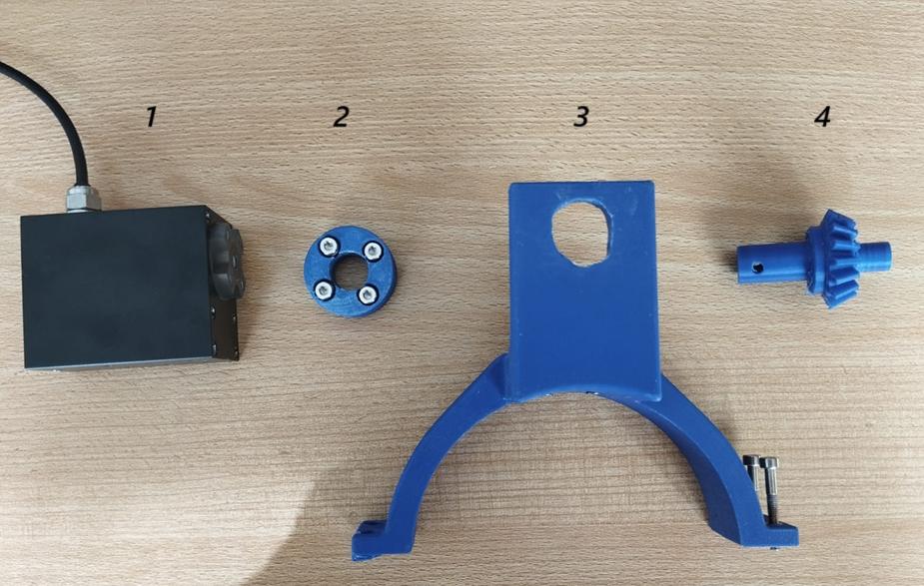
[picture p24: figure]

Figure 1 : Pièces composant une attache moteur

Chaque moteur est fixé individuellement à son support en suivant les étapes ci-dessous :
- Assembler la pièce 2 sur la pièce 1 à l’aide de quatre vis M4 de 12 mm.
- Monter cet ensemble sur la pièce 3 à l’aide de quatre vis coniques M3 de 16 mm.
- Fixer la pièce 4 à l’ensemble à l’aide d’une vis M4 de 40 mm et d’un écrou. Cette dernière pièce peut nécessiter un léger montage en force.
Répéter cette opération quatre fois, pour chacun des servomoteurs.

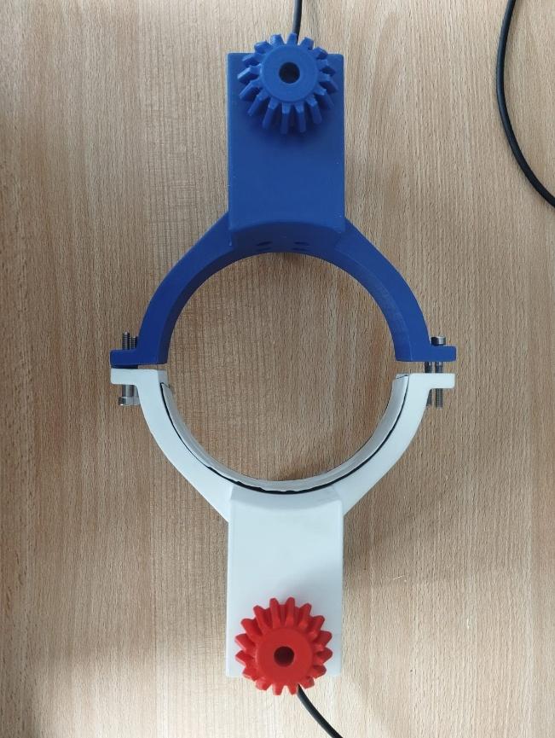
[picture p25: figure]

Figure 2 : Montage d'une paire d'attaches moteurs
Former ensuite deux paires de moteurs comme illustré sur la photo, en les assemblant à l’aide de quatre vis et écrous M4 de 30 mm. Veiller à laisser un espace suffisant entre les deux brides de fixation pour pouvoir ensuite les enfiler autour du tube central.

## 2. Montage sur le tube central

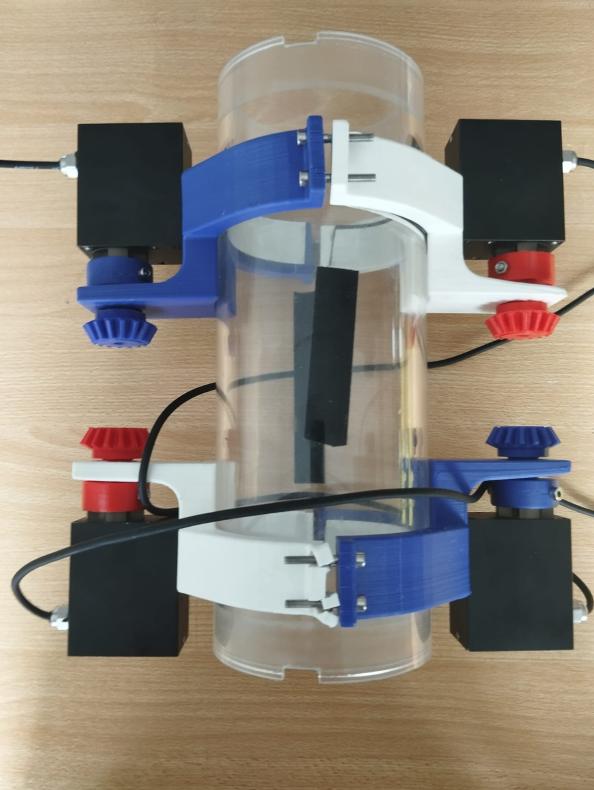
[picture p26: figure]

Figure 3 : Positionnement des paires d'attaches moteurs sur le tube

Enfiler la première paire de moteurs autour du tube en polycarbonate, en insérant au préalable les bandes de caoutchouc entre les clamps et le tube afin d’assurer une meilleure accroche. Positionner le tube à la verticale, posé sur une table, et placer la première paire à la base, moteurs orientés vers le bas (reposant sur la table).
Fixer solidement cette paire pour éviter tout mouvement.
Enfiler ensuite la deuxième paire par le haut du tube. Cette dernière doit être orientée de manière à ce que les moteurs soient placés à l’extrémité supérieure du robot.

## 3. Montage des ailes

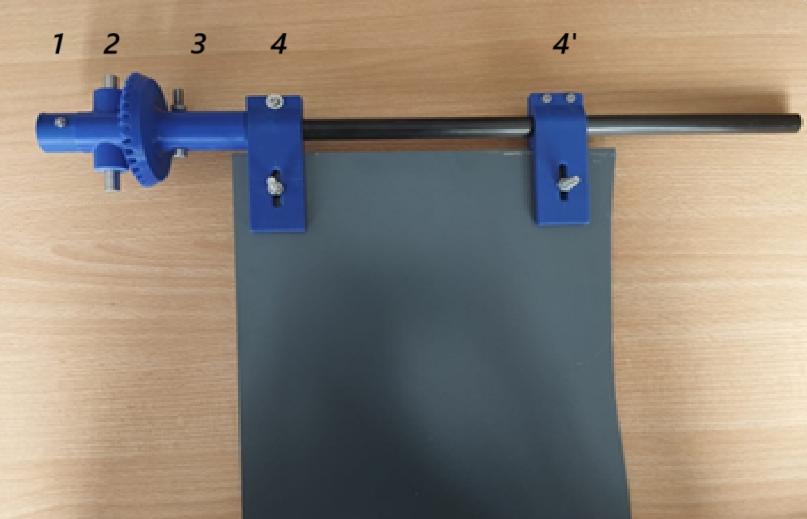
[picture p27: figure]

Figure 4 : Pièces composant une seule aile

Chaque aile est montée en suivant les étapes ci-dessous :
- Fixer la pièce 1 sur le tube en carbone à l’aide d’une vis M3 de 35 mm.
- Enfiler ensuite la pièce 2 sur ce même tube.
- Fixer la pièce 3 à l’aide d’une vis M5 de 35 mm.
- Assembler les pièces 4 et 4’ sur les plaques de PVC, à l’aide de vis M5 de 25 mm.
- Enfin, fixer l’aile complète sur le tube de carbone à l’aide de quatre vis M3 de 20 mm. Répéter l’opération pour assembler la seconde aile.

## 4. Montage final de l’ensemble

Avant d’assembler les différents modules, il est essentiel de positionner les servomoteurs à 180°.
Pour cela :
- Connecter les servos conformément au schéma électrique fourni.
- Lancer le code général : les moteurs se placeront automatiquement à la position 180°.

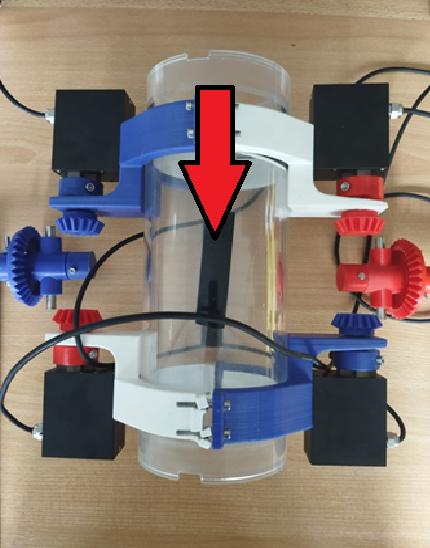
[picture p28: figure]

Figure 5 : Positionnement de l'ensemble des pièces lors de l'assemblage final

Une fois les moteurs positionnés :
- Positionner les ailes à l’endroit souhaité, de manière symétrique et alignée par rapport à l’axe du robot.
- Faire coulisser la paire supérieure de moteurs jusqu’à ce qu’elle vienne emboîter et maintenir les ailes.
- Veiller à maintenir l’alignement précis des moteurs et des ailes pendant cette étape pour éviter tout décalage ou contrainte mécanique. (Voir figure 6 pour l’alignement des ailes)

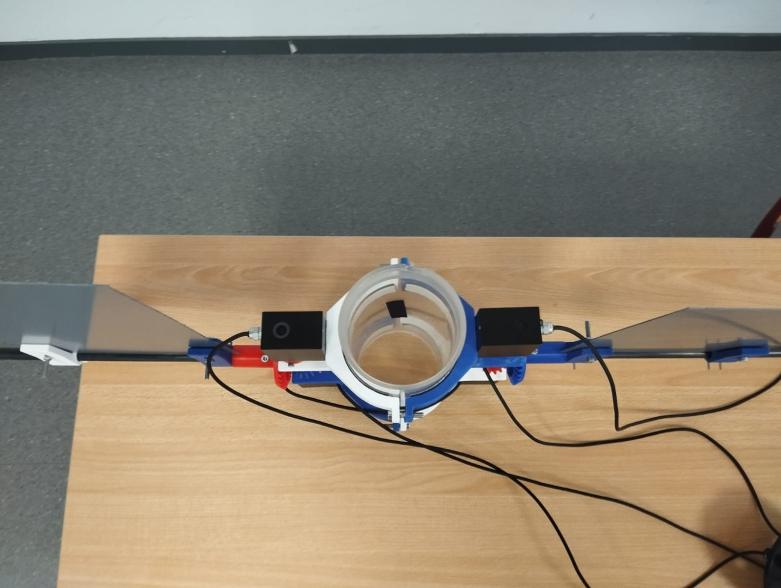
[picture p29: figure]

Figure 6 : Position des ailes lors de l'assemblage final

## 5. Étanchéité et finalisation

Le montage mécanique est à présent terminé. Il ne reste plus qu’à :
- Connecter les câbles des servomoteurs via les pénétrateurs WetLink.
- Assurer l’étanchéité du tube principal selon les recommandations de Blue Robotics. Pour cela, suivre précisément les guides suivants disponibles sur le site de Blue Robotics :
- Watertight Enclosure User Guide (https://bluerobotics.com/learn/watertight-enclosure-wte-assembly-new/)
- WetLink Penetrator Installation Guide – Blue Robotics (https://bluerobotics.com/learn/wetlink-penetrator-installation-guide/)
Ce montage constitue la base mécanique du prototype raie voilier. Il est désormais prêt à recevoir les composants électroniques embarqués et à être testé en environnement contrôlé.

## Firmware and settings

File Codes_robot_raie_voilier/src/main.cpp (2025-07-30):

#include "Differential.h"
#include "DifferentialGroup.h"
#include "DifferentialServer.h"

Differential diff1(9, 6, 0, 360); // Configuration de la premiére epaule sur les pin 9 et 6
Differential diff2(3, 5, 0, 360); // Configuration de la seconde epaule sur les pin 3 et 5
DifferentialGroup group(diff1, diff2);
DifferentialServer server(80);


void setup() {
    Serial.begin(9600);
    Serial.println("Démarrage OK");

    server.begin();

    // Initialisation des quatres servo a la position 180
    diff1.setup();
    diff2.setup();
}

void loop() {

    int a, b, c, d, e, f, mode =0;

    while (true) {

        if (server.update(a, b, c, d, e, f, mode)) { // a = angle translation (degrés), b = angle rotation (degrés), c = periode en radiant/seconde, d = dephasage entre les deux ailes, e/f = pourcentage de la periode que prend le temps de monté/descante 
            Serial.print("Reçu : ");
            // Serial.print(a); Serial.print(", ");
            // Serial.print(b); Serial.print(", ");
            // Serial.print(c); Serial.print(", ");
            // Serial.print(d); Serial.print(", ");
            // Serial.print(e); Serial.print(", ");
            // Serial.print(f); Serial.print(", ");
            // Serial.println(mode);*
        }
        
        if (mode == 0) ;

        else if (mode == 1) group.sinusoideTranslationSynchronisee(a, c, d);

        else if (mode == 2) group.sinusoideRotationSynchronisee(a, c, d);

        else if (mode == 3) group.sinusoideCombineeSynchronisee(a, b, c, d);

        else if (mode == 4) group.carreLisserotationMontDescIndependants(a, c, d, e, f);
        
        else if (mode == 5) group.carreLisseTranslationMontDescIndependants(a, c, d, e, f);

        else if (mode == 6) group.carreLisseTranslationMontDescIndependantsAdoucis(a, c, d, e, f);

        else if (mode == 7) {
            diff1.voilier();
            diff2.voilier();
            delay(7000);
            diff1.voilierdescente();
            diff2.voilierdescente();

            delay(100000);

        }

    }
// tests sans la comuunication

//   group.sinusoideTranslationSynchronisee(45, 120, 0);
//   group.sinusoideRotationSynchronisee(45, 40, 0);
//   group.sinusoideCombineeSynchronisee(45, 45, 120, 0);
//   group.carreLisserotationMontDescIndependants(30, 60, 0, 0.2, 0.2);
//   group.carreLisseTranslationMontDescIndependants(30.0, 60.0, 0.0, 0.1, 0.1);
//   group.carreLisseTranslationMontDescIndependants(30.0, 60.0, 0.0, 0.3, 0.3);

}











// import requests

// def envoyer_valeurs(v1, v2, v3, v4, v5):
//     url = f"http://192.168.1.2/cmd/{v1}/{v2}/{v3}/{v4}/{v5}"
//     try:
//         r = requests.get(url, timeout=2)
//         print("Réponse Arduino :", r.text.strip())
//     except requests.exceptions.RequestException as e:
//         print("Erreur :", e)

// envoyer_valeurs(45, 45, 40, 3, 0)

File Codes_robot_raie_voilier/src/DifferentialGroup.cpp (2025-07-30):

#include "DifferentialGroup.h"

DifferentialGroup::DifferentialGroup(Differential& d1, Differential& d2)
    : diff1(d1), diff2(d2) {}

void DifferentialGroup::sinusoideTranslationSynchronisee(float amplitudeDeg, float vitesseDegPerSec, float phaseShiftRad) {
    float amplitudeServo = amplitudeDeg * 2;
    float omega = vitesseDegPerSec / amplitudeDeg;
    float period = 2 * M_PI / omega;

    const unsigned long dt_ms = 5;
    unsigned long startMillis = millis();

    while ((millis() - startMillis) / 1000.0 < period) {
        float t = (millis() - startMillis) / 1000.0;
        float angle1 = amplitudeServo * sin(omega * t);
        float angle2 = amplitudeServo * sin(omega * t + phaseShiftRad);

        int base1a = (diff1.angleMin + diff1.angleMax) / 2 + angle1 / 2;
        int base1b = (diff1.angleMin + diff1.angleMax) / 2 - angle1 / 2;
        int base2a = (diff2.angleMin + diff2.angleMax) / 2 + angle2 / 2;
        int base2b = (diff2.angleMin + diff2.angleMax) / 2 - angle2 / 2;

        diff1.setServos(constrain(base1a, diff1.angleMin, diff1.angleMax),
                        constrain(base1b, diff1.angleMin, diff1.angleMax));
        diff2.setServos(constrain(base2a, diff2.angleMin, diff2.angleMax),
                        constrain(base2b, diff2.angleMin, diff2.angleMax));

        delay(dt_ms);
    }
}
    

void DifferentialGroup::sinusoideRotationSynchronisee(float amplitudeDeg, float vitesseDegPerSec, float phaseShiftRad) {
    const float rapportReductionRotation = 4.0;
    float amplitudeServo = amplitudeDeg * rapportReductionRotation;
    float omega = vitesseDegPerSec / amplitudeDeg;
    float period = 2 * M_PI / omega;

    const unsigned long dt_ms = 5;
    unsigned long startMillis = millis();

    while ((millis() - startMillis) / 1000.0 < period) {
        float t = (millis() - startMillis) / 1000.0;
        float angle1 = amplitudeServo * sin(omega * t);
        float angle2 = -amplitudeServo * sin(omega * t + phaseShiftRad);  // Inversion du signal ici

        int base1 = (diff1.angleMin + diff1.angleMax) / 2 + angle1 / 2;
        int base2 = (diff2.angleMin + diff2.angleMax) / 2 + angle2 / 2;

        diff1.setServos(constrain(base1, diff1.angleMin, diff1.angleMax),
                        constrain(base1, diff1.angleMin, diff1.angleMax));
        diff2.setServos(constrain(base2, diff2.angleMin, diff2.angleMax),
                        constrain(base2, diff2.angleMin, diff2.angleMax));

        delay(dt_ms);
    }
}


void DifferentialGroup::sinusoideCombineeSynchronisee(float amplitudeTranslationDeg, float amplitudeRotationDeg, float vitesseDegPerSec, float phaseShiftRad) {
    const float rapportReductionRotation = 4.0;

    float amplitudeServoTranslation = amplitudeTranslationDeg * 2;
    float amplitudeServoRotation = amplitudeRotationDeg * rapportReductionRotation;
    float omega = vitesseDegPerSec / max(amplitudeTranslationDeg, amplitudeRotationDeg);
    float period = 2 * M_PI / omega;

    const unsigned long dt_ms = 5;
    unsigned long startMillis = millis();

    while ((millis() - startMillis) / 1000.0 < period) {
        float t = (millis() - startMillis) / 1000.0;

        float angleTranslation1 = amplitudeServoTranslation * sin(omega * t);
        float angleRotation1 = -amplitudeServoRotation * sin(omega * t);  // inversion ici

        float angleTranslation2 = amplitudeServoTranslation * sin(omega * t + phaseShiftRad);
        float angleRotation2 = amplitudeServoRotation * sin(omega * t + phaseShiftRad);

        int pos1a = (diff1.angleMin + diff1.angleMax) / 2 + (angleRotation1 / 2) + (angleTranslation1 / 2);
        int pos1b = (diff1.angleMin + diff1.angleMax) / 2 + (angleRotation1 / 2) - (angleTranslation1 / 2);
        int pos2a = (diff2.angleMin + diff2.angleMax) / 2 + (angleRotation2 / 2) + (angleTranslation2 / 2);
        int pos2b = (diff2.angleMin + diff2.angleMax) / 2 + (angleRotation2 / 2) - (angleTranslation2 / 2);

        diff1.setServos(constrain(pos1a, diff1.angleMin, diff1.angleMax),
                        constrain(pos1b, diff1.angleMin, diff1.angleMax));
        diff2.setServos(constrain(pos2a, diff2.angleMin, diff2.angleMax),
                        constrain(pos2b, diff2.angleMin, diff2.angleMax));

        delay(dt_ms);
    }
}




void DifferentialGroup::carreLisserotationMontDescIndependants(float amplitudeDeg, float vitesseDegPerSec, float phaseShiftRad, float dureeMontee, float dureeDescente) {
    const float rapportReductionRotation = 4.0;
    float amplitudeServo = amplitudeDeg * rapportReductionRotation;

    float omega = vitesseDegPerSec / amplitudeDeg;
    float period = 2 * M_PI / omega;
    float demiPeriode = period / 2.0;

    float plateauHaut = demiPeriode - dureeMontee;
    float plateauBas  = demiPeriode - dureeDescente;

    const unsigned long dt_ms = 5;
    unsigned long startMillis = millis();

    auto signalLisse = [&](float tCycle, float plateau, float dureeTransition, bool isMontee) -> float {
        if (tCycle < plateau) {
            return isMontee ? 1.0 : -1.0;
        } else if (tCycle < plateau + dureeTransition) {
            float ratio = (tCycle - plateau) / dureeTransition;
            return isMontee ? (1.0 - 2.0 * ratio) : (-1.0 + 2.0 * ratio);
        } else {
            return isMontee ? -1.0 : 1.0;
        }
    };

    while ((millis() - startMillis) / 1000.0 < period) {
        float t = (millis() - startMillis) / 1000.0;

        float t1 = fmod(t, period);
        float t2 = fmod(t + phaseShiftRad / omega, period); 

        float signal1, signal2;

        if (t1 < demiPeriode) {
            signal1 = signalLisse(t1, plateauHaut, dureeMontee, true);
        } else {
            signal1 = signalLisse(t1 - demiPeriode, plateauBas, dureeDescente, false);
        }

        if (t2 < demiPeriode) {
            signal2 = signalLisse(t2, plateauHaut, dureeMontee, true);
        } else {
            signal2 = signalLisse(t2 - demiPeriode, plateauBas, dureeDescente, false);
        }

        signal2 = -signal2;

        float angle1 = amplitudeServo * signal1;
        float angle2 = amplitudeServo * signal2;

        int base1 = (diff1.angleMin + diff1.angleMax) / 2 + angle1 / 2;
        int base2 = (diff2.angleMin + diff2.angleMax) / 2 + angle2 / 2;

        diff1.setServos(constrain(base1, diff1.angleMin, diff1.angleMax),
                        constrain(base1, diff1.angleMin, diff1.angleMax));
        diff2.setServos(constrain(base2, diff2.angleMin, diff2.angleMax),
                        constrain(base2, diff2.angleMin, diff2.angleMax));

        delay(dt_ms);
    }
}
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
